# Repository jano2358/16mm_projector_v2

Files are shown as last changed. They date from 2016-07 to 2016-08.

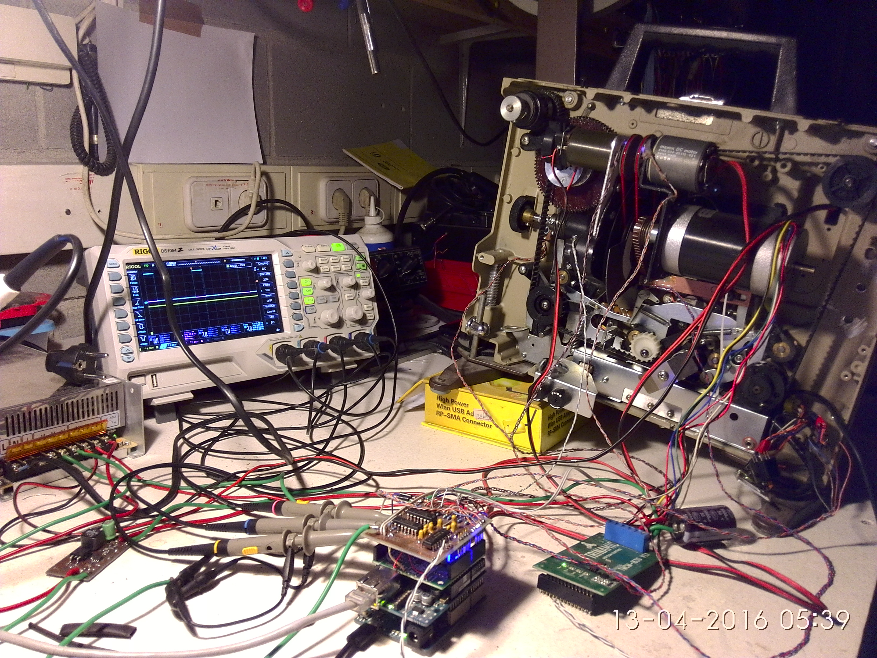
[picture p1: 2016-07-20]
photo_n_video/gen_view_unassembled.jpg

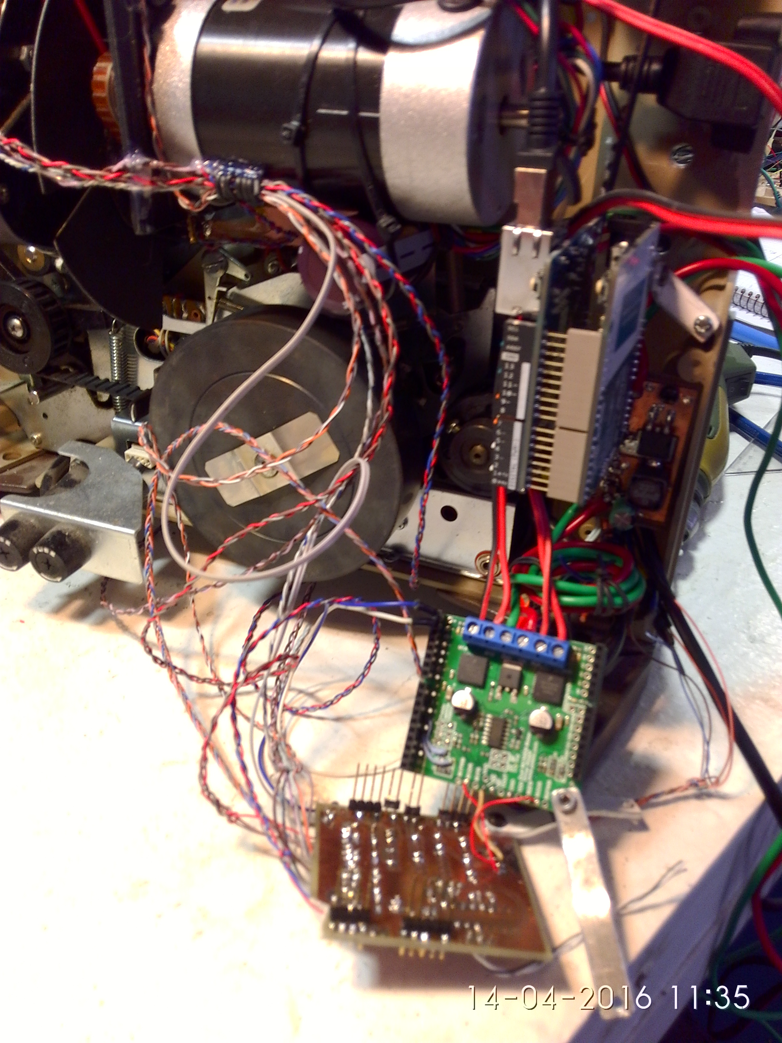
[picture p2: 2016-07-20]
photo_n_video/control_disassembly.jpg

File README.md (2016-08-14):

# 16mm_projector_v2
mod of a 16mm projector for the project "El curso del tiempo" from Xavi Hurtado

This is a modification of a projector (EIKI SSL0L) to take control over the parameters of the projection: tape speed, amount of light and shutter.
For the light we replace the incandescent bulb (300W, lumens: unknown)  by a COB LED (Citizen CLU058-1825C4-303M2K1, 100W about 17000 lumen).
To control the tape speed, We replaced the original motor with a DC brushless servo motor (Trinamic QBL5704-94-04-032 and TMCM-1630 control board).
The shutter originaly was hard linked to the main motor, we eliminated the hard link to have control independant, added a secondary shutter and two DC motors to move them. The link to the main motor and sync was made by a dual PLL system programed on an Arduino M0 board.
The power for these DC motors is delivered trough a Pololu board dual MC33296.
Arduino also controls the communication with the TMCM-1630 trough serial interface, the amount of light by switching the LED with a power
mosfet and receive the control from the computer over an ethernet line in OSC packets (we use here the Arduino Ethernet 2 Wiznet W5500).
The power is supplied by a Mean Well RSP-500-48 raised to 54V, with two DC-DC converters based on the TPS54560 chip from TI.

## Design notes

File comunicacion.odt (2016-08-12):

Variables de entrada:

Nombre | Tipo | Rango | Utilidad
/Vel_main | Int o Float | -43~43 (fps) | Velocidad del motor de arrastre, medida en frames por segundo
/Luz | Int | 0~255 | Potencia enviada a la lampara LED
/Vel_front | Int o Float | 0~150 (ops) | Velocidad del obturador frontal cuando es libre, medida en obturaciones por segundo.
/Vel_tras | Int o Float | 0~150 (ops) | Velocidad del obturador trasero cuando es libre.
/Master_front_tras | Int o Boolean | 0~1 | 0: el maestro del motor del obturador frontal es el Main 1: el maestro es el motor del obturador trasero
/Master_tras_front | Int o Boolean | 0~1 | 0: el maestro del motor del obturador trasero es el Main 1: el maestro es el motor del obturador frontal
/Front_free | Int o Boolean | 0~1 | 0: el motor del obturador frontal es esclavo 1: el motor es libre
/Tras_free | Int o Boolean | 0~1 | 0: el motor del obturador trasero es esclavo 1: el motor es libre
/Front_park | Int o Boolean | 0~1 | 0: indiferente 1: el motor del obturador frontal no es esclavo y se lleva a la posicion de parking.
/Tras_park | Int o Boolean | 0~1 | 0: indiferente 1: el motor del obturador trasero no es esclavo y se lleva a la posicion de parking.
/Div_front | Int o Float | 0~3 | Factor por el que se multiplicara la velocidad del motor del obturador frontal con respecto al maestro
/Div_tras | Int o Float | 0~3 | Factor por el que se multiplicara la velocidad del motor del obturador trasero con respecto al maestro
/Ph_f_target | Int o Float | 0~359 | Relacion de fase deseada para el motor del obturador frontal con respecto al maestro
/Ph_t_target | Int o Float | 0~359 | Relacion de fase desdeada para el motor del obturador trasero con respecto al maestro

Como acuse de dato recibido se retorna el mismo dato, en el caso de la velocidad del motor de arrastre de la cinta el dato se devuelve una vez que la placa Trinamic haya retornado los datos confirmados.

Los datos recibidos y retornados son del tipo OSC Message. El puerto de recepcion es 8000 y el de respuesta el 6000, la IP sera 172.26.100.177

Datos retornados cada 100mS:

Nombre | Tipo | Utilidad
/vel_obt_front_act | Float | Velocidad actual del obturador frontal
/vel_obt_tras_act | Float | Velocidad actual del obturador trasero
/ph_diff_front_act | Float | Diferencia de fase del obturador frontal actual respecto a su maestro.
/ph_diff_tras_act | Float | Diferencia de fase del obturador trasero actual respecto a su maestro.
/frame_count | Float | Cuenta de los cuadros pasados

Descripcion del sistema de control de los motores que mueven los obturadores:

El bloque de control basico es un sistema de lazo cerrado alimentando un PID con la velocidad deseada y la velocidad actual medida en la interrupcion correspondiente (estas interrupciones tienen una tasa de 11 pulsos por revolucion y son medidas en la polea solidaria con el motor en cuestion), la salida de PID es aplicada al PWM que alimenta el puente H de cada motor.

El siguiente nivel de control es un segundo lazo de realimentacion que tiene como entrada el resultado de la diferencia de tiempo entre el motor que sera esclavizado y su maestro, la salida se suma a la entrada de PID, en este caso los parametros Ki, Kp y Kd de PID estaran ajustados en una relacion aproximada 22:1 integral con respecto a proporcional, conformando un filtro de paso bajo. Si pensamos en el motor como un oscilador controlado por voltaje (PWM), la medicion de diferencia de tiempo es efectivamente un comparador de fase y la PID ajustada como filtro de paso bajo, el conjunto se puede ver como un PLL.

Uno de los tiempos que entran en el comparador de fase se multiplicara por un factor (/Div_front y /Div_tras respectivamente) para obtener una velocidad multiplicada como resultado pudiendo controlar de esta manera velocidades relativas al master diferentes a la unidad.

Un tercer lazo de realimentacion existe entre, la diferencia del tiempo medido directamente en cada obturador y el medido en quien sea su master, esta diferencia es expresada en grados (0~360) y sumada al tiempo que se le resta del maestro para obtener el error de la comparacion de entrada a PID, manejando una peticion de error en ese valor (entradas /Ph_f_target y /Ph_t_target)

conseguiremos un 'angulo' sumado al de referencia que proporciona el maestro. Este angulo se supervisa en el main loop y se corrige cuando se obtiene el valor de tiempo en cuestion.

Para seleccionar los estados se han colocado switches logicos con los que se permite seleccionar el origen de datos para el esclavo (/Master_tras front y /Master_front_tras) y si el motor en cuestion es libre o esclavo (/Front_free y /Tras_free), si el motor es libre el control sera su entrada de peticion de velocidad (/Vel_front y /Vel_tras).

Notas de utilizacion:

- la relacion de fase se mantiene con decencia en todo el rango central, en los extremos se puede perder la linealidad creando un bucle infinito de busqueda de fase, se recomienda mantener la fase en un rango 10º < Ph_x_target < 350º, en caso de que entre en bucle se puede salir de el con un requerimiento de fase un poco mas distanciado del extremo util

- la fase de entrada de los obturadores en pantalla es de180º para el obturador frontal y 170º para el obturador trasero, esto es medido con respecto al flanco de subida de la señal de sincronia del eje de arrastre de la cinta que coincide con el momento en el que se ha depositado un cuadro en la zona de proyeccion y la uña de arrastre va a por el siguiente

- a bajas velocidades las inercias del sistema son mas dificiles de controlar y afectan a la sincronia, tambien la tasa de datos se vuelve insuficiente hasta 6fps se soporta bien, por debajo de 5fps ya no es suficiente, si la sincronia desdeada es entre los obturadores, éste limite esta sobre los 12ops

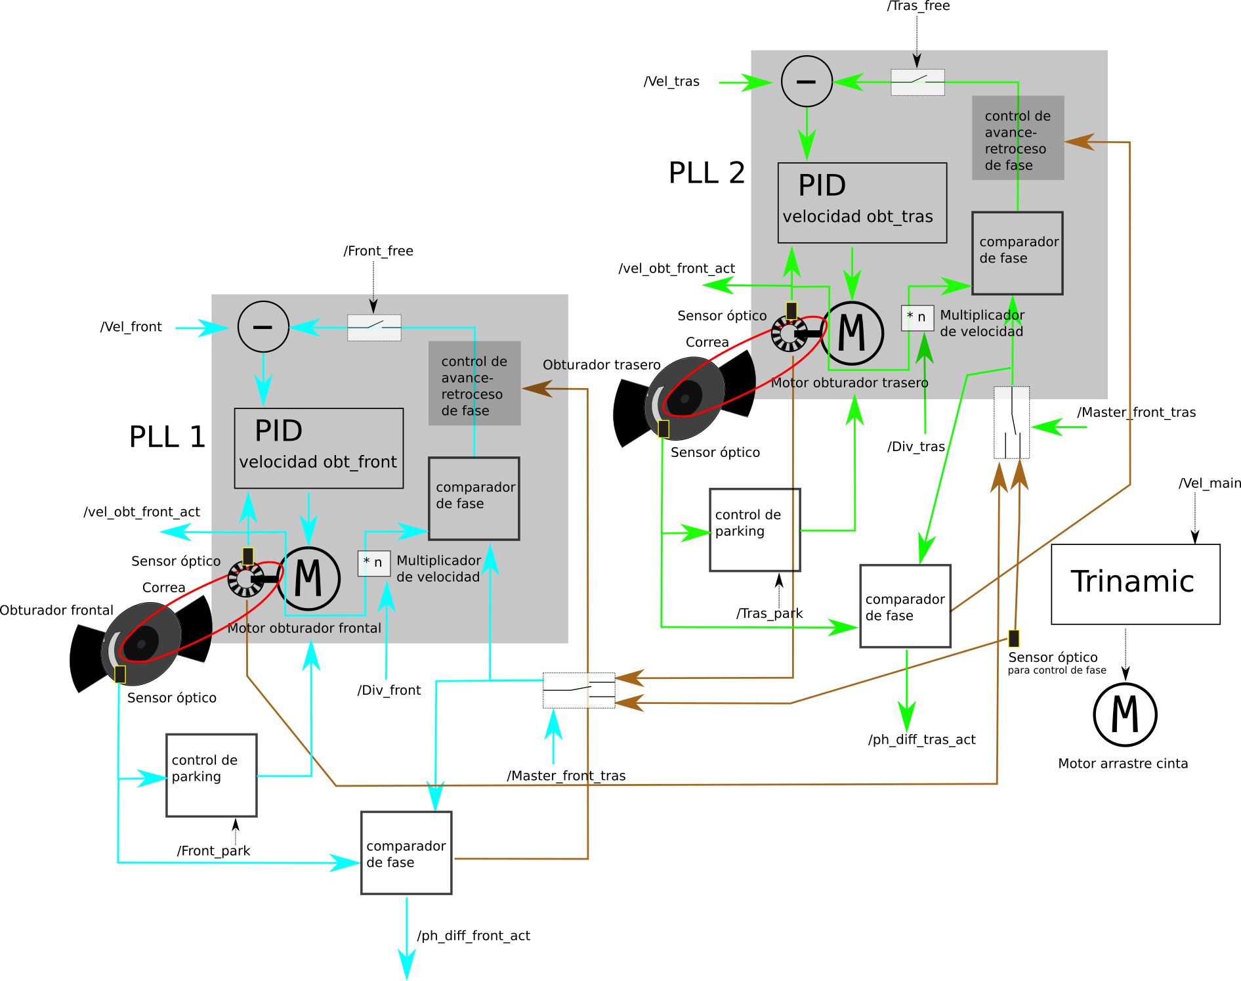
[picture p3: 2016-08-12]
Diagrama_de_bloques_0_2.png

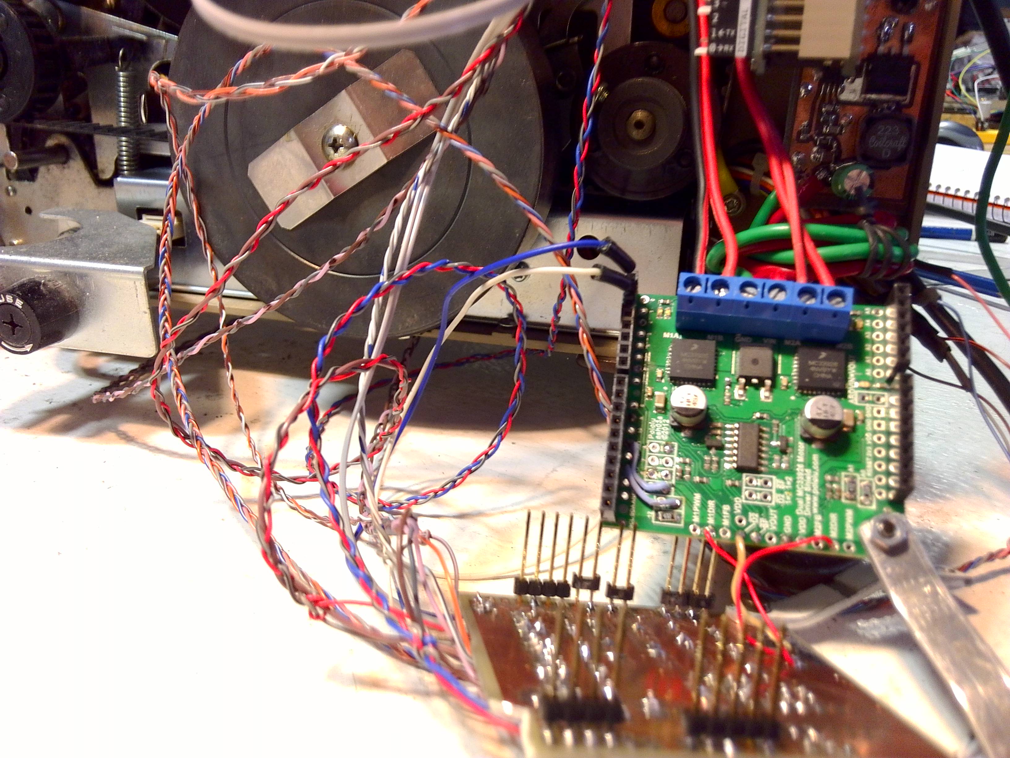
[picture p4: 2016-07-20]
photo_n_video/pololu_motor_control.jpg

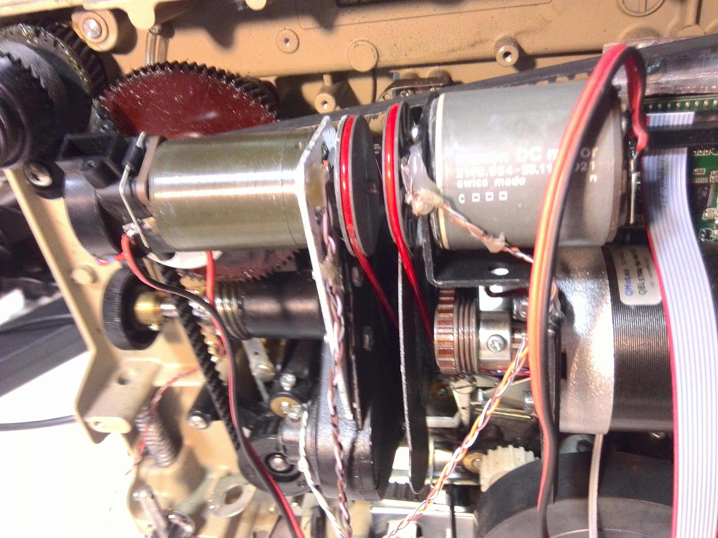
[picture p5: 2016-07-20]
photo_n_video/motors_close.jpg

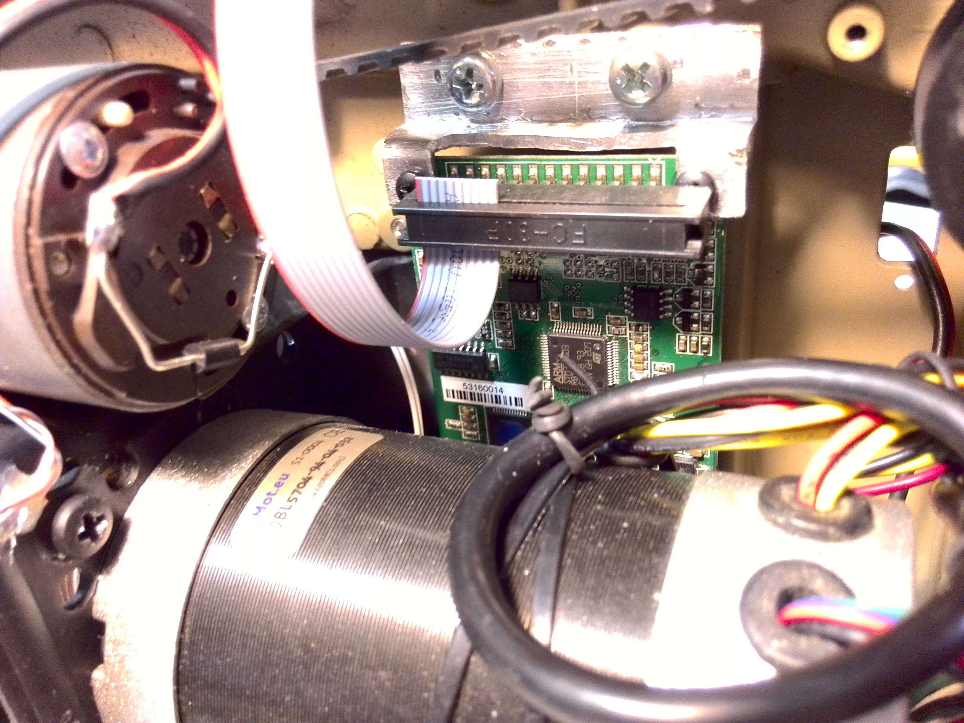
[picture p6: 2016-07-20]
photo_n_video/trinamic_board.jpg

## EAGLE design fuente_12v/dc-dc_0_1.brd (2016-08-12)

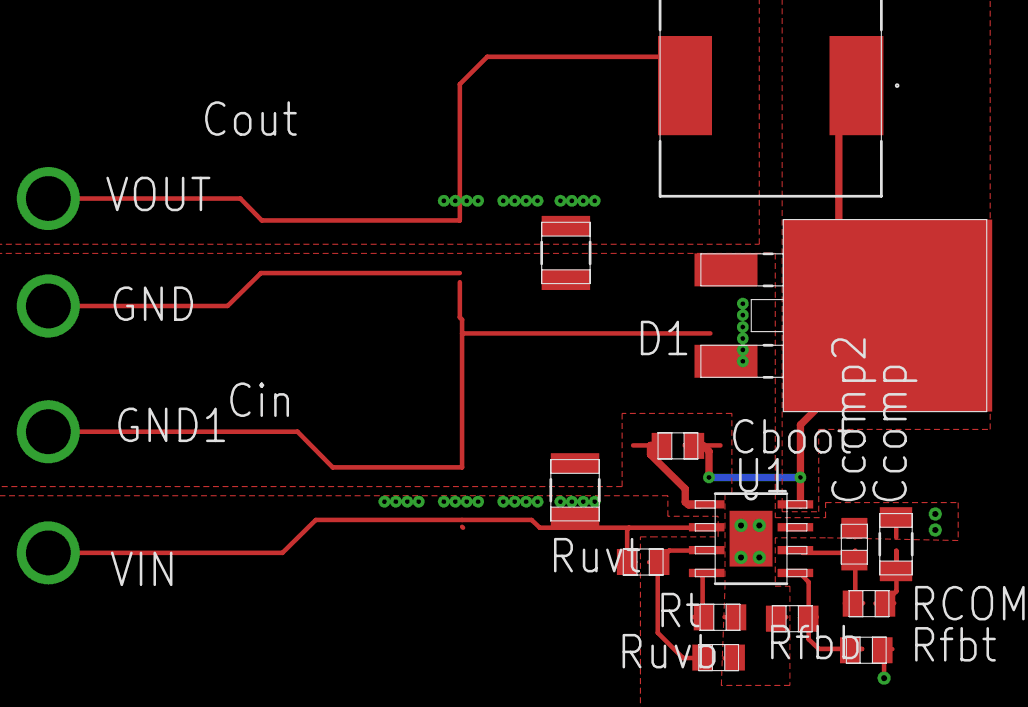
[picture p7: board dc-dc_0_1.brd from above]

Board: 4 copper layers, 18 parts (0 on the bottom side), 10 nets.

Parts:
Cboot: 0805
Ccomp: 1206
Ccomp2: 0805
Cin: 1210
Cout: 1210_280
D1: DDPAK
GND, GND1: TP-1502
L1: MSS1210
RCOMP: 0805
Rfbb: 0805
Rfbt: 0805
Rt: 0805
Ruvb: 0805
Ruvt: 0805
U1: R-PDSO-G8
VIN: TP-1502
VOUT: TP-1502

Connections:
0: Ccomp.2, Ccomp2.2, Cin.2, Cout.2, D1.1, D1.3, GND.1, GND1.1, Rfbb.2, Rt.2, Ruvb.2, U1.7, U1.9
1: Ccomp2.1, RCOMP.2, U1.6
2: Rt.1, U1.4
3: Cboot.1, U1.1
4: Rfbb.1, Rfbt.2, U1.5
5: Cboot.2, D1.2, L1.1, U1.8
6: Cin.1, Ruvt.1, U1.2, VIN.1
7: Cout.1, L1.2, Rfbt.1, VOUT.1
20: Ccomp.1, RCOMP.1
29: Ruvb.1, Ruvt.2, U1.3

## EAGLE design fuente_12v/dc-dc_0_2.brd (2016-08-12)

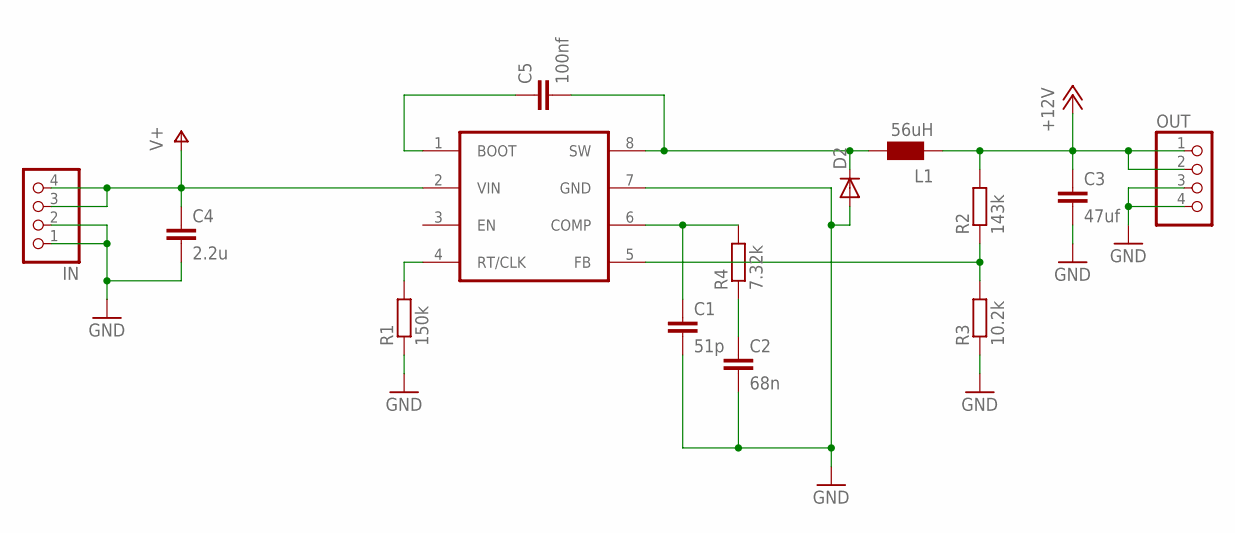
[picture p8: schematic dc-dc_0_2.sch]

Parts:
C1: 51p; C0805
C2: 68n; C1206
C3: 47uf; C1210
C4: 2.2u; C1210
C5: 100nf; C0805
D2: DIODE-DO-214AC; DO-214AC
IN: PINHD-1X4; 1X04
L1: 56uH; WE-PD_L/XL/XXL
OUT: PINHD-1X4; 1X04
R1: 150k; R0805
R2: 143k; R0805
R3: 10.2k; R0805
R4: 7.32k; R0805
U1: TPS54560; SO08-POWERPAD

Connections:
+12V: C3.1, L1.2 (1), OUT.1, OUT.2, R2.2
GND: C1.2, C2.2, C3.2, C4.2, D2.A, IN.1, IN.2, OUT.3, OUT.4, R1.1, R3.1, U1.7 (GND)
unnamed: C5.1, U1.1 (BOOT)
unnamed: C5.2, D2.C, L1.1 (2), U1.8 (SW)
unnamed: R2.1, R3.2, U1.5 (FB)
unnamed: C1.1, R4.2, U1.6 (COMP)
unnamed: C2.1, R4.1
unnamed: R1.2, U1.4 (RT/CLK)
V+: C4.1, IN.3, IN.4, U1.2 (VIN)

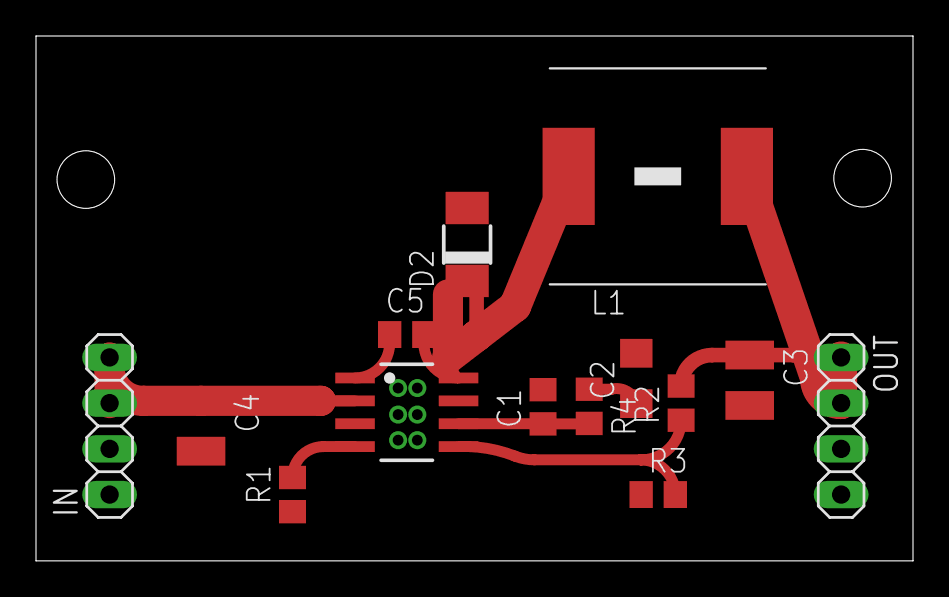
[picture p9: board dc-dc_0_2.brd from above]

Board: 2 copper layers, 48.7 x 29.2 mm, 14 parts (0 on the bottom side), 9 nets.

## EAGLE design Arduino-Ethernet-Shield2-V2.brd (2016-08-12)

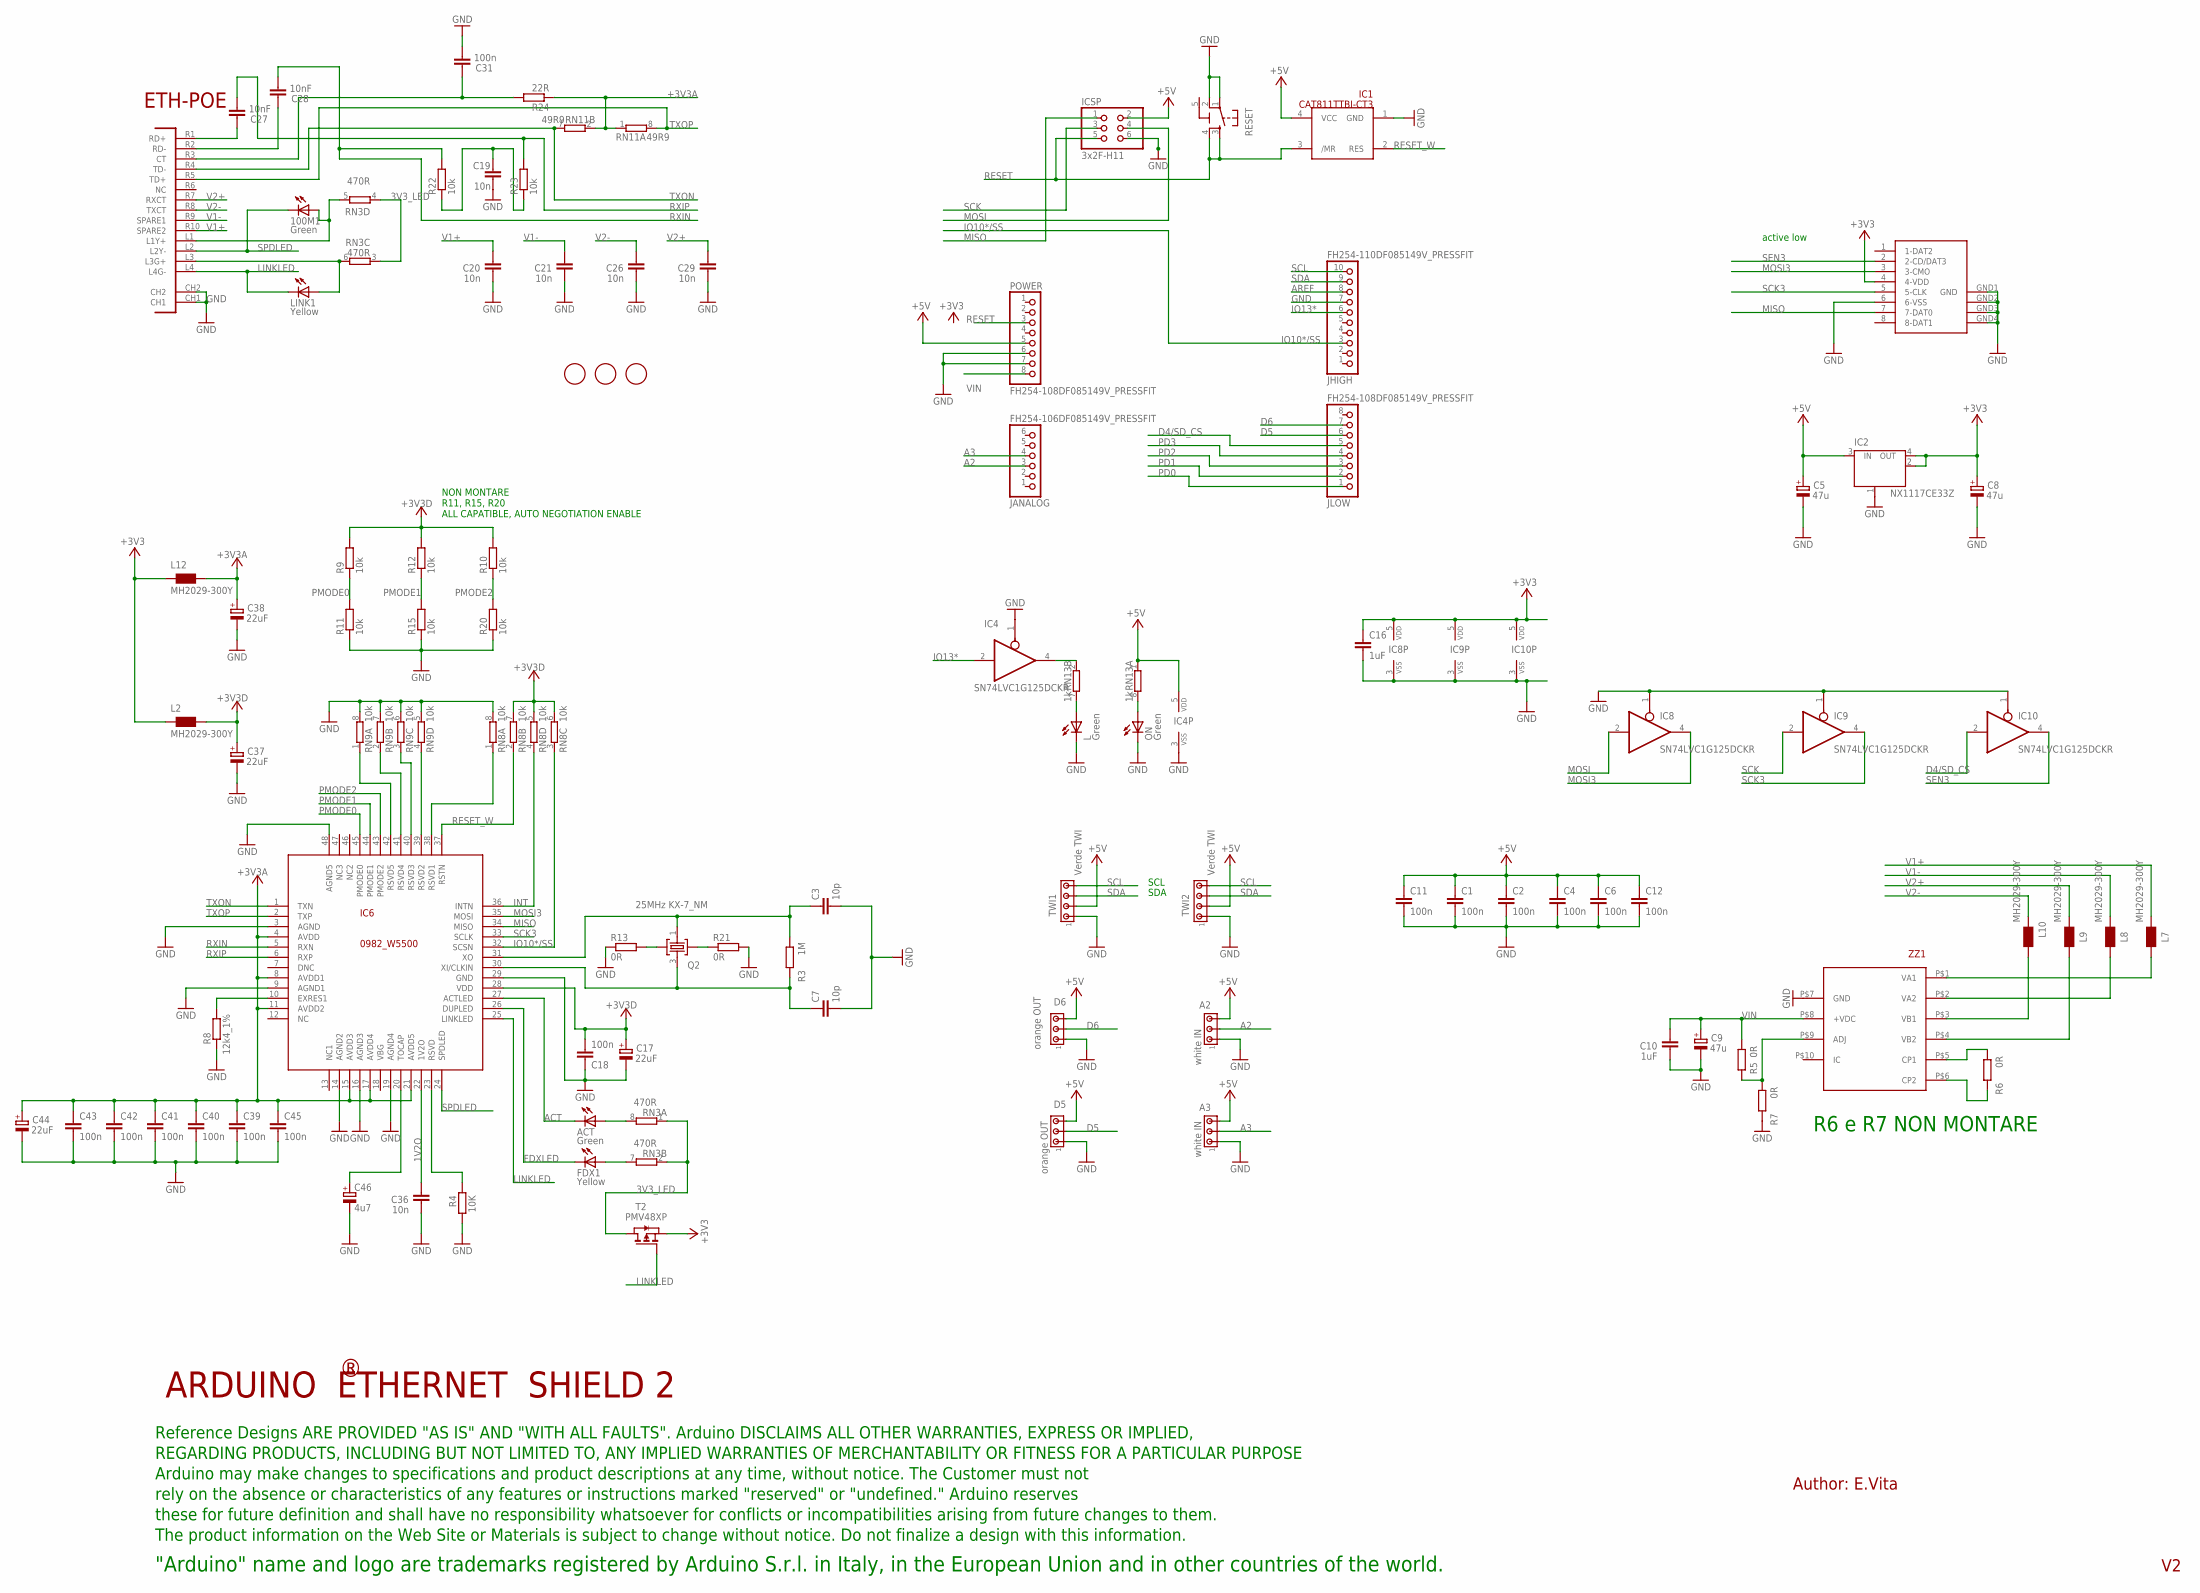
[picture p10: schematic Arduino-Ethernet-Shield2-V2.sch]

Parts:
100M1: Green; CHIPLED_0805
A2, A3: white IN; 10X03MTA
ACT: Green; CHIPLED_0805
C1, C2, C4, C6, C11, C12, C18, C31, C39, C40, C41, C42, C43, C45: 100n; C0603-ROUND
C3, C7: 10p; C0603-ROUND
C5, C8, C9: 47u; PANASONIC_D
C10, C16: 1uF; C0603-ROUND
C17, C37, C38, C44: 22uF; SMC_B
C19, C20, C21, C26, C29, C36: 10n; C0603-ROUND
C27, C28: 10nF; C0603-ROUND
C46: 4u7; SMC_A
D5, D6: orange OUT; 10X03MTA
FDX1: Yellow; CHIPLED_0805
FID2, FID3, FID4: FIDUCIALMOUNT; FIDUCIA-MOUNT
IC1: CAT811TTBI-CT3; SOT143
IC2: NX1117CE33Z; SOT223
IC4, IC8, IC9, IC10: SN74LVC1G125DCKR; SC70-5
IC6: 0982_W5500; TQFP48-7X7
ICSP: 3x2F-H11; 2X03
JANALOG: FH254-106DF085149V_PRESSFIT; 1X06-TH-PRESSFIT
JHIGH: FH254-110DF085149V_PRESSFIT; 1X10-TH-PRESSFIT
JLOW: FH254-108DF085149V_PRESSFIT; 1X08-TH-PRESSFIT
L: Green; CHIPLED_0805
L2, L7, L8, L9, L10, L12: MH2029-300Y; 0805
LINK1: Yellow; CHIPLED_0805
ON: Green; CHIPLED_0805
POWER: FH254-108DF085149V_PRESSFIT; 1X08-TH-PRESSFIT
Q2: 25MHz KX-7_NM; CRYSTAL3.2X2.5
R3: 1M; R0603-ROUND
R4: 10K; R0603-ROUND
R5, R6, R7: 0R; R0603-ROUND
R8: 12k4_1%; R0603-ROUND
R9, R10, R11, R12, R15, R20, R22, R23: 10k; R0603-ROUND
R13, R21: 0R; R0402
R24: 22R; R0603-ROUND
RESET: 0946_TS42031-160W-TR-7260; TS42
RN3: 470R; CAY16
RN8, RN9: 10k; CAY16
RN11: 49R9; CAY16
RN13: 1k; CAY16
T2: PMV48XP; SOT-23; PART_NUMBER PMV48XP
TWI1, TWI2: Verde TWI; 10X04MTA
U$1: DISCLAIMER
UC1: RB1-125BHQ1A; POE-RJ45
X1: 0046_15TW-882; SDCARD-15TW-8821
ZZ1: 0343_AG9612-2BR; AG9000

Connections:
1V2O: C36.2, IC6.22 (1V2O)
3V3_LED: RN3.1, RN3.2 (1), RN3.3 (1), RN3.4 (1), T2.1 (D)
5-GND: RESET.5 (5-GND)
+3V3: C8.+, C16.1, IC2.2 (OUT), IC2.4 (OUT), IC8.5 (VDD), IC9.5 (VDD), IC10.5 (VDD), L2.1, L12.1, T2.2 (S), X1.4 (4-VDD)
+3V3A: C38.+, C39.1, C40.1, C41.1, C42.1, C43.1, C44.+, C45.1, IC6.4 (AVDD), IC6.8 (AVDD1), IC6.11 (AVDD2), IC6.15 (AVDD3), IC6.17 (AVDD4), IC6.21 (AVDD5), L12.2, R24.1, RN11.1, RN11.2 (1)
+3V3D: C17.+, C18.2, C37.+, IC6.28 (VDD), L2.2, R9.2, R10.2, R12.2, RN8.5 (2), RN8.6 (2), RN8.7 (2)
+5V: A2.3, A3.3, C1.1, C2.1, C4.1, C5.+, C6.1, C11.1, C12.1, D5.3, D6.3, IC1.4 (VCC), IC2.3 (IN), IC4.5 (VDD), ICSP.2, POWER.5, RN13.1, TWI1.2, TWI2.2
A2: A2.2, JANALOG.3
A3: A3.2, JANALOG.4
ACT: ACT.C, IC6.27 (ACTLED)
AREF: JHIGH.8
D4/SD_CS: IC10.2 (I), JLOW.5
D5: D5.2, JLOW.6
D6: D6.2, JLOW.7
FDXLED: FDX1.C, IC6.26 (DUPLED)
GND: A2.1, A3.1, C1.2, C2.2, C3.2, C4.2, C5.-, C6.2, C7.2, C8.-, C9.-, C10.1, C11.2, C12.2, C16.2, C17.-, C18.1, C19.1, C20.1, C21.1, C26.1, C29.1, C31.1, C36.1, C37.-, C38.-, C39.2, C40.2, C41.2, C42.2, C43.2, C44.-, C45.2, C46.-, D5.1, D6.1, IC1.1 (GND), IC2.1 (GND/ADJ), IC4.1 (OE), IC4.3 (VSS), IC6.3 (AGND), IC6.9 (AGND1), IC6.14 (AGND2), IC6.16 (AGND3), IC6.19 (AGND4), IC6.29 (GND), IC6.48 (AGND5), IC8.1 (OE), IC8.3 (VSS), IC9.1 (OE), IC9.3 (VSS), IC10.1 (OE), IC10.3 (VSS), ICSP.6, JHIGH.7, L.C, ON.C, POWER.6, POWER.7, R4.1, R7.2, R8.1, R11.1, R13.1, R15.1, R20.1, R21.2, RESET.1, RESET.2, RN8.8 (2), RN9.5 (2), RN9.6 (2), RN9.7 (2), RN9.8 (2), TWI1.1, TWI2.1, UC1.CH1, UC1.CH2, X1.6 (6-VSS), X1.GND1 (GND), X1.GND2 (GND1), X1.GND3 (GND2), X1.GND4 (GND3), ZZ1.P$7 (GND)
INT: IC6.36 (INTN), RN8.4 (1)
IO10*/SS: IC6.32 (SCSN), JHIGH.3, RN8.3 (1)
IO13*: IC4.2 (I), JHIGH.6
LINKLED: IC6.25 (LINKLED), LINK1.C, T2.3 (G), UC1.L4 (L4G-)
MISO: IC6.34 (MISO), ICSP.1, X1.7 (7-DAT0)
MOSI: IC8.2 (I), ICSP.4
MOSI3: IC6.35 (MOSI), IC8.4 (O), X1.3 (3-CMO)
unnamed: L7.2, ZZ1.P$1 (VA1)
unnamed: L8.2, ZZ1.P$2 (VA2)
unnamed: L9.2, ZZ1.P$4 (VB2)
unnamed: L10.2, ZZ1.P$3 (VB1)
unnamed: C3.1, IC6.31 (XO), Q2.1, R3.1
unnamed: IC6.39 (RSVD2), RN9.4 (1)
unnamed: ACT.A, RN3.8 (2)
unnamed: Q2.2, R13.2
unnamed: Q2.4, R21.1
unnamed: LINK1.A, RN3.6 (2), UC1.L3 (L3G+)
unnamed: IC6.23 (RSVD), R4.2
unnamed: 100M1.A, RN3.5 (2), UC1.L1 (L1Y+)
unnamed: C19.2, R22.1, R23.1
unnamed: C27.2, UC1.R1 (RD+)
unnamed: C28.2, UC1.R2 (RD-)
unnamed: FDX1.A, RN3.7 (2)
unnamed: IC6.40 (RSVD3), RN9.3 (1)
unnamed: R6.1, ZZ1.P$5 (CP1)
unnamed: R6.2, ZZ1.P$6 (CP2)
unnamed: R5.2, R7.1, ZZ1.P$9 (ADJ)
unnamed: IC6.41 (RSVD4), RN9.2 (1)
unnamed: C31.2, R24.2, UC1.R3 (CT)
unnamed: IC6.42 (RSVD5), RN9.1
unnamed: C46.+, IC6.20 (TOCAP)
unnamed: IC6.38 (RSVD1), RN8.1
unnamed: IC6.10 (EXRES1), R8.2
unnamed: ON.A, RN13.8 (2)
unnamed: IC4.4 (O), RN13.2 (1)
unnamed: L.A, RN13.7 (2)
NC: IC6.12 (NC)
OSC2E2: C7.1, IC6.30 (XI/CLKIN), Q2.3, R3.2
PD0: JLOW.1
PD1: JLOW.2
PD2: JLOW.3
PD3: JLOW.4
PMODE0: IC6.45 (PMODE0), R9.1, R11.2
PMODE1: IC6.44 (PMODE1), R12.1, R15.2
PMODE2: IC6.43 (PMODE2), R10.1, R20.2
RESET: IC1.3 (/MR), ICSP.5, POWER.3, RESET.3, RESET.4
RESET_W: IC1.2 (RES), IC6.37 (RSTN), RN8.2 (1)
RXIN: C28.1, IC6.5 (RXN), R22.2
RXIP: C27.1, IC6.6 (RXP), R23.2
SCK: IC9.2 (I), ICSP.3
SCK3: IC6.33 (SCLK), IC9.4 (O), X1.5 (5-CLK)
SCL: JHIGH.10, TWI1.4, TWI2.4
SDA: JHIGH.9, TWI1.3, TWI2.3
SEN3: IC10.4 (O), X1.2 (2-CD/DAT3)
SPDLED: 100M1.C, IC6.24 (SPDLED), UC1.L2 (L2Y-)
TXON: IC6.1 (TXN), RN11.7 (2), UC1.R4 (TD-)
TXOP: IC6.2 (TXP), RN11.8 (2), UC1.R5 (TD+)
V1+: C20.2, L7.1, UC1.R10 (SPARE2)
V1-: C21.2, L8.1, UC1.R9 (SPARE1)
V2+: C29.2, L9.1, UC1.R7 (RXCT)
V2-: C26.2, L10.1, UC1.R8 (TXCT)
VIN: C9.+, C10.2, POWER.8, R5.1, ZZ1.P$8 (+VDC)

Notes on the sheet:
active low
NON MONTARE R11, R15, R20 ALL CAPATIBLE, AUTO NEGOTIATION ENABLE
ETH-POE
SCL
SDA
R6 e R7 NON MONTARE
ARDUINO ETHERNET SHIELD 2
Author: E.Vita

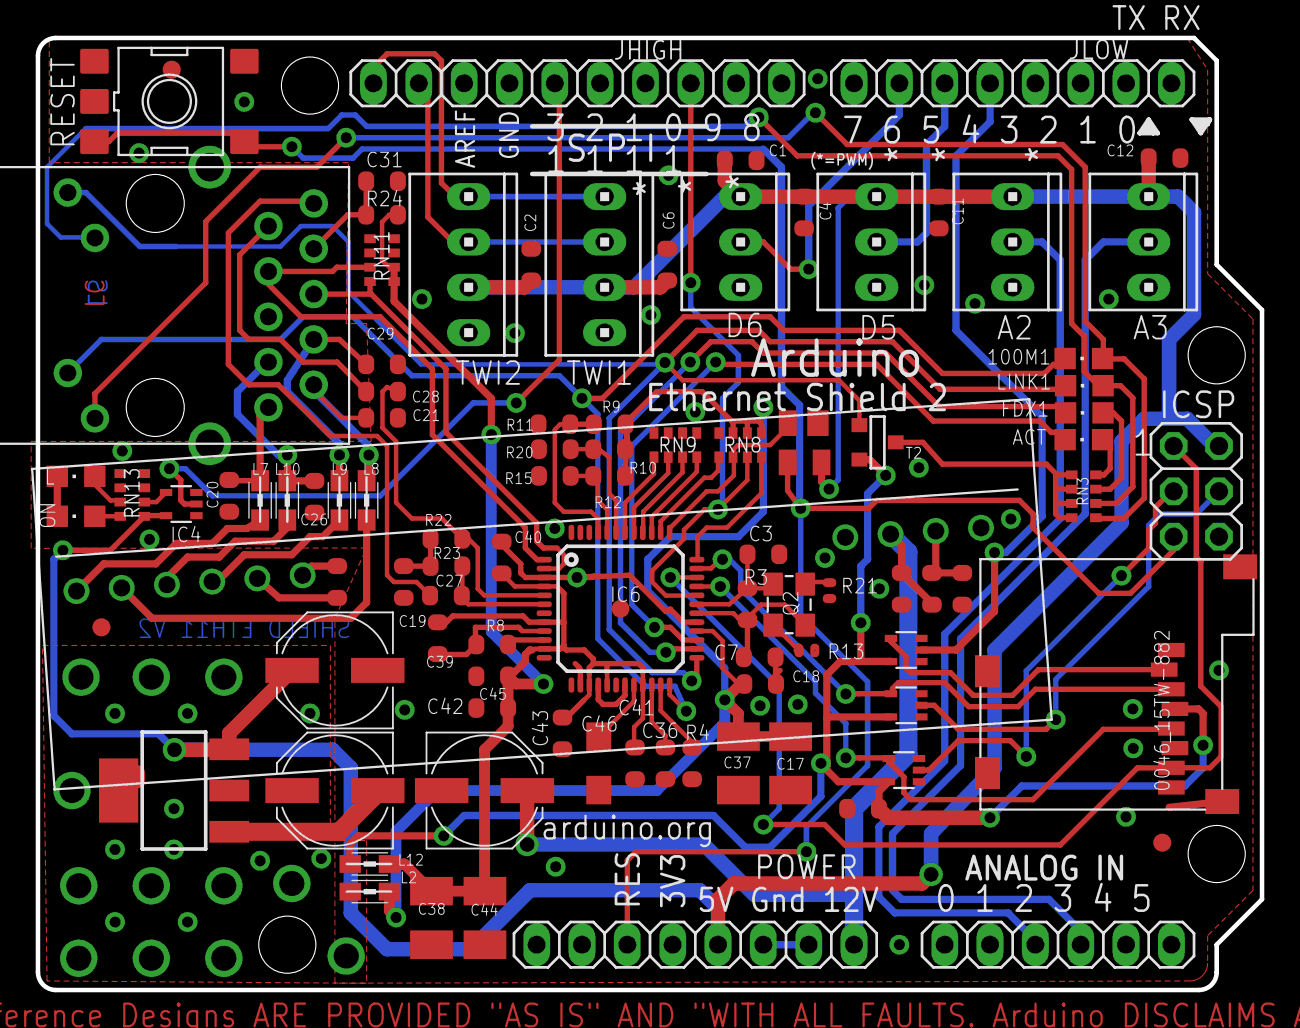
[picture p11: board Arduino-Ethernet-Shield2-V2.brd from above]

Board: 2 copper layers, 68.6 x 53.3 mm, 96 parts (0 on the bottom side), 71 nets.

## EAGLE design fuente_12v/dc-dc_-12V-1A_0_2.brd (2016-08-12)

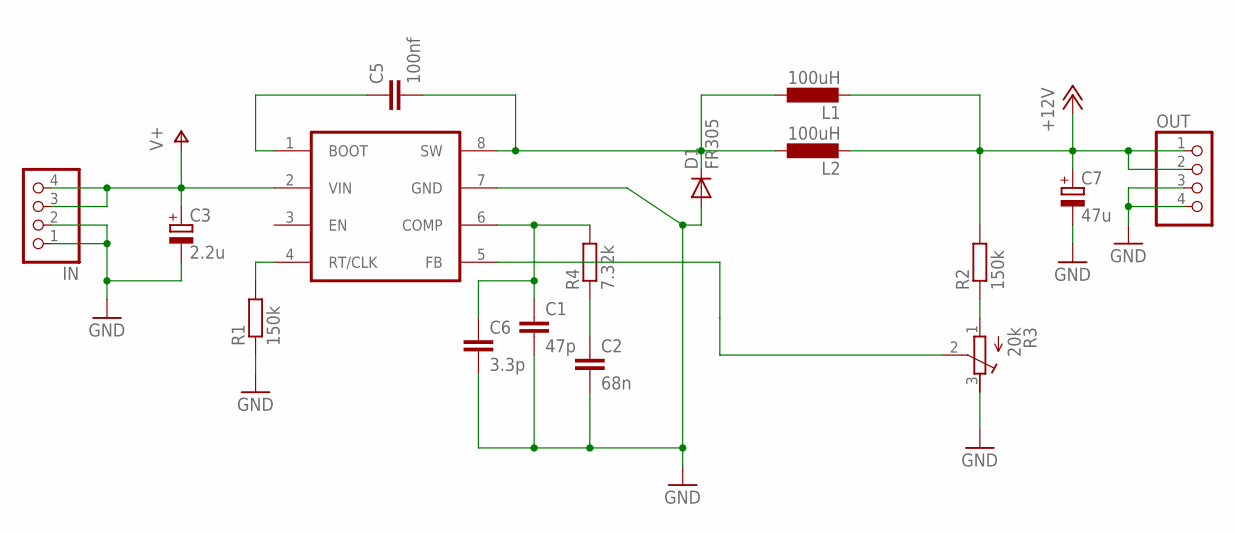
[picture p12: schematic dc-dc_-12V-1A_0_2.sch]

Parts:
C1: 47p; C1206
C2: 68n; C1206
C3: 2.2u; E2-4
C5: 100nf; C0805
C6: 3.3p; C1206
C7: 47u; E2-4
D1: FR305; DO201-15
IN: PINHD-1X4; 1X04
L1, L2: 100uH; RCL_6000-XXXX-RC
OUT: PINHD-1X4; 1X04
R1, R2: 150k; R0805
R3: 20k; RTRIM64X
R4: 7.32k; 0204/5
U1: TPS54560; SO08-POWERPAD

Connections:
+12V: C7.+, L1.2, L2.2, OUT.1, OUT.2, R2.2
GND: C1.2, C2.2, C3.-, C6.2, C7.-, D1.A, IN.1, IN.2, OUT.3, OUT.4, R1.1, R3.3 (A), U1.7 (GND)
unnamed: C5.1, U1.1 (BOOT)
unnamed: C5.2, D1.C, L1.1, L2.1, U1.8 (SW)
unnamed: R2.1, R3.1 (E)
unnamed: R3.2 (S), U1.5 (FB)
unnamed: C1.1, C6.1, R4.2, U1.6 (COMP)
unnamed: C2.1, R4.1
unnamed: R1.2, U1.4 (RT/CLK)
V+: C3.+, IN.3, IN.4, U1.2 (VIN)

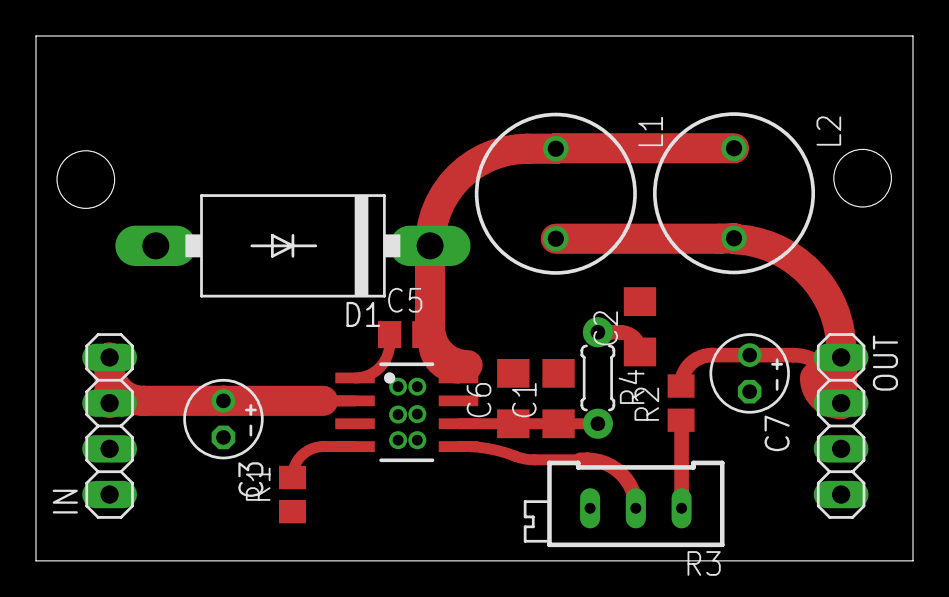
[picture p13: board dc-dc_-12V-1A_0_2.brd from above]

Board: 2 copper layers, 48.7 x 29.2 mm, 16 parts (0 on the bottom side), 10 nets.

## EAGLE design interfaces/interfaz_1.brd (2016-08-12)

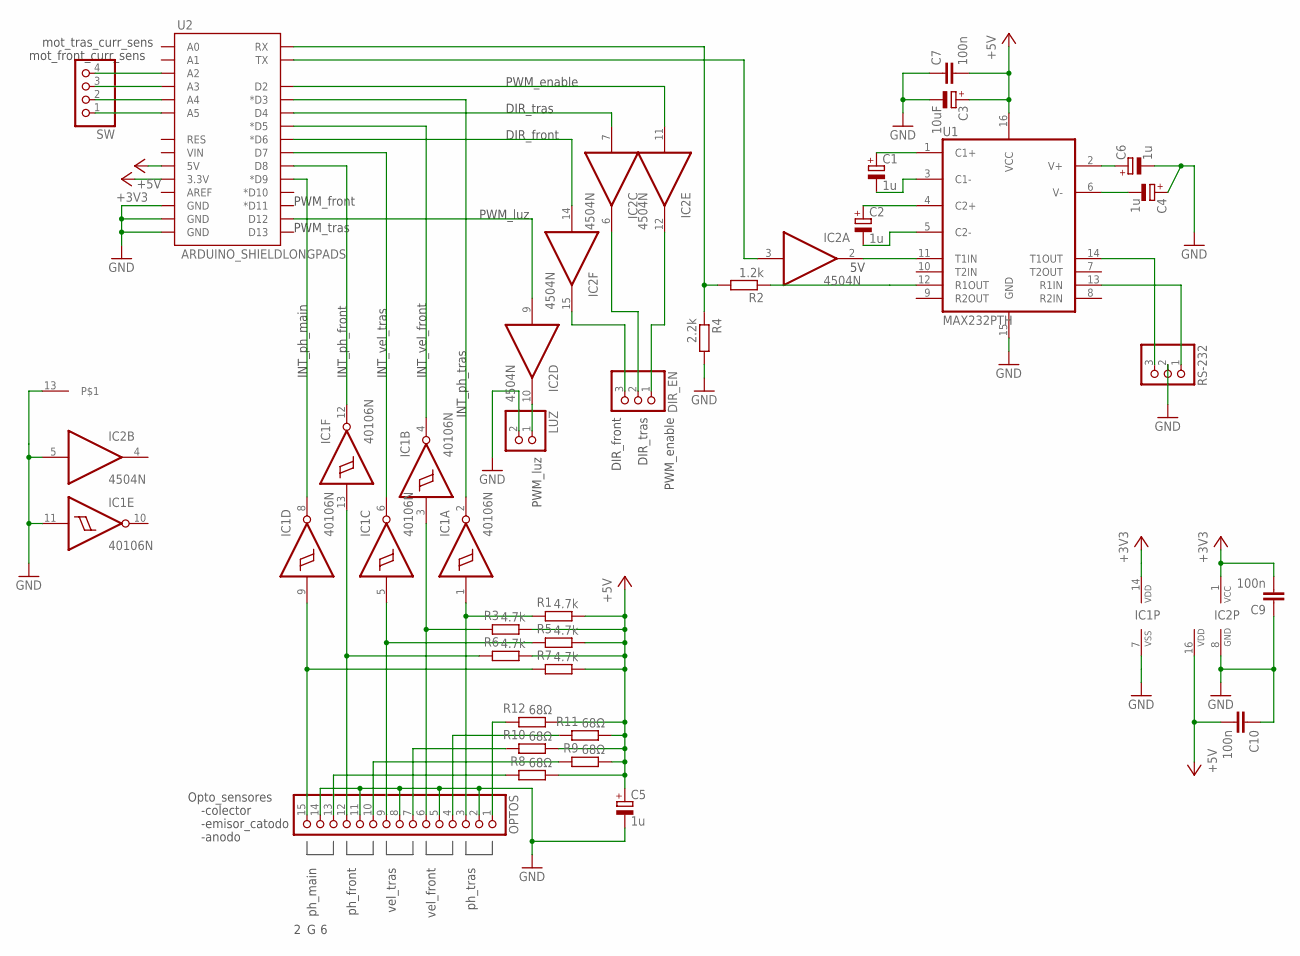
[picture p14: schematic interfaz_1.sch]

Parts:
C1, C2, C4, C5, C6: 1u; E2-4
C3: 10uF; E2-4
C7, C9, C10: 100n; C025-025X050
DIR_EN: PINHD-1X3; 1X03
IC1: 40106N; DIL14
IC2: 4504N; DIL16
LUZ: PINHD-1X2; 1X02
OPTOS: PINHD-1X15; 1X15
R1, R3, R5, R6, R7: 4.7k; 0204/5
R2: 1.2k; 0204/5
R4: 2.2k; 0204/5
R8, R9, R10, R11, R12: 68Ω; 0204/5
RS-232: PINHD-1X3; 1X03
SW: PINHD-1X4; 1X04
U1: MAX232PTH; DIL16
U2: ARDUINO_SHIELDLONGPADS; DUEMILANOVE_SHIELD_LONGPADS

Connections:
+3V3: C9.2, IC1.14 (VDD), IC2.1 (VCC), U2.3.3V
+5V: C3.+, C5.+, C7.2, C10.2, IC2.16 (VDD), R1.1, R3.1, R5.1, R6.1, R7.1, R8.1, R9.1, R10.1, R11.1, R12.1, U1.16 (VCC), U2.5V
GND: C3.-, C4.+, C5.-, C6.-, C7.1, C9.1, C10.1, IC1.7 (VSS), IC1.11 (I), IC2.5 (I), IC2.8 (GND), IC2.13, LUZ.2, OPTOS.2, OPTOS.5, OPTOS.8, OPTOS.11, OPTOS.14, R4.2, RS-232.2, U1.15 (GND), U2.GND@0 (GND), U2.GND@1 (GND), U2.GND@2 (GND)
unnamed: C1.+, U1.1 (C1+)
unnamed: C1.-, U1.3 (C1-)
unnamed: C2.+, U1.4 (C2+)
unnamed: C2.-, U1.5 (C2-)
unnamed: C4.-, U1.6 (V-)
unnamed: C6.+, U1.2 (V+)
unnamed: RS-232.1, U1.13 (R1IN)
unnamed: IC2.11 (I), U2.D2
unnamed: IC2.3 (I), U2.TX
unnamed: R2.1, U1.12 (R1OUT)
unnamed: R2.2, R4.1, U2.RX
unnamed: IC2.2 (O), U1.11 (T1IN)
unnamed: DIR_EN.1, IC2.12 (O)
unnamed: RS-232.3, U1.14 (T1OUT)
unnamed: IC2.7 (I), U2.D4
unnamed: DIR_EN.2, IC2.6 (O)
unnamed: IC2.14 (I), U2.D6 (*D6)
unnamed: DIR_EN.3, IC2.15 (O)
unnamed: IC2.9 (I), U2.D12
unnamed: IC2.10 (O), LUZ.1
unnamed: IC1.3 (I), OPTOS.6, R3.2
unnamed: IC1.2 (O), U2.D3 (*D3)
unnamed: IC1.4 (O), U2.D5 (*D5)
unnamed: IC1.6 (O), U2.D7
unnamed: IC1.12 (O), U2.D8
unnamed: IC1.8 (O), U2.D9 (*D9)
unnamed: IC1.1 (I), OPTOS.3, R1.2
unnamed: IC1.5 (I), OPTOS.9, R5.2
unnamed: IC1.13 (I), OPTOS.12, R6.2
unnamed: IC1.9 (I), OPTOS.15, R7.2
unnamed: OPTOS.13, R8.2
unnamed: OPTOS.10, R9.2
unnamed: OPTOS.7, R10.2
unnamed: OPTOS.4, R11.2
unnamed: OPTOS.1, R12.2
unnamed: SW.1, U2.A5
unnamed: SW.2, U2.A4
unnamed: SW.3, U2.A3
unnamed: SW.4, U2.A2

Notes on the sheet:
PWM_enable
DIR_tras
DIR_front
PWM_luz
PWM_tras
PWM_front
INT_vel_tras
INT_vel_front
INT_ph_tras
INT_ph_front
INT_ph_main
Opto_sensores
-colector
-emisor_catodo
-anodo
ph_main
ph_front
ph_tras
vel_front
vel_tras
mot_tras_curr_sens
mot_front_curr_sens

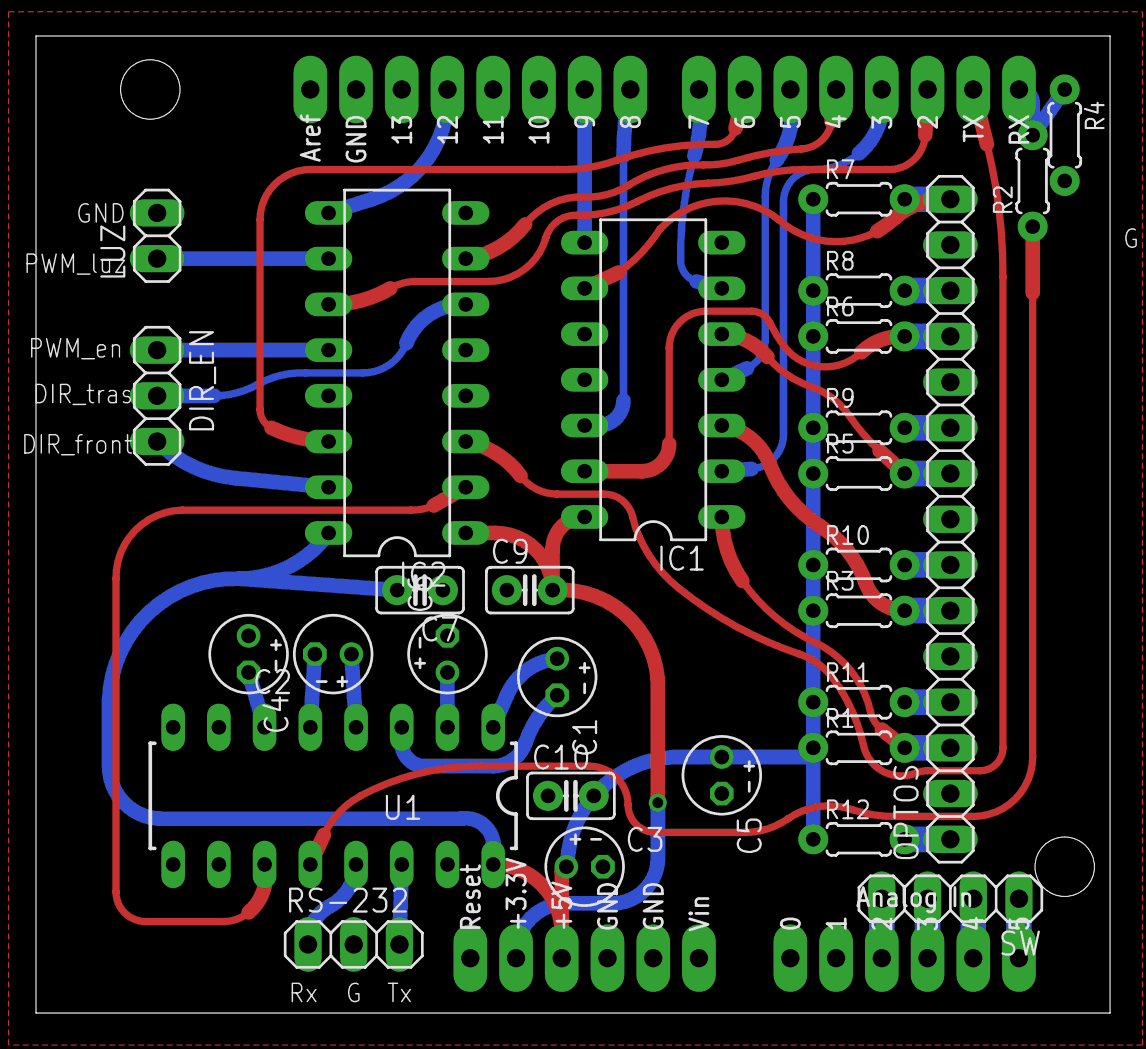
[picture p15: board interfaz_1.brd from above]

Board: 2 copper layers, 59.7 x 54.3 mm, 30 parts (0 on the bottom side), 42 nets.

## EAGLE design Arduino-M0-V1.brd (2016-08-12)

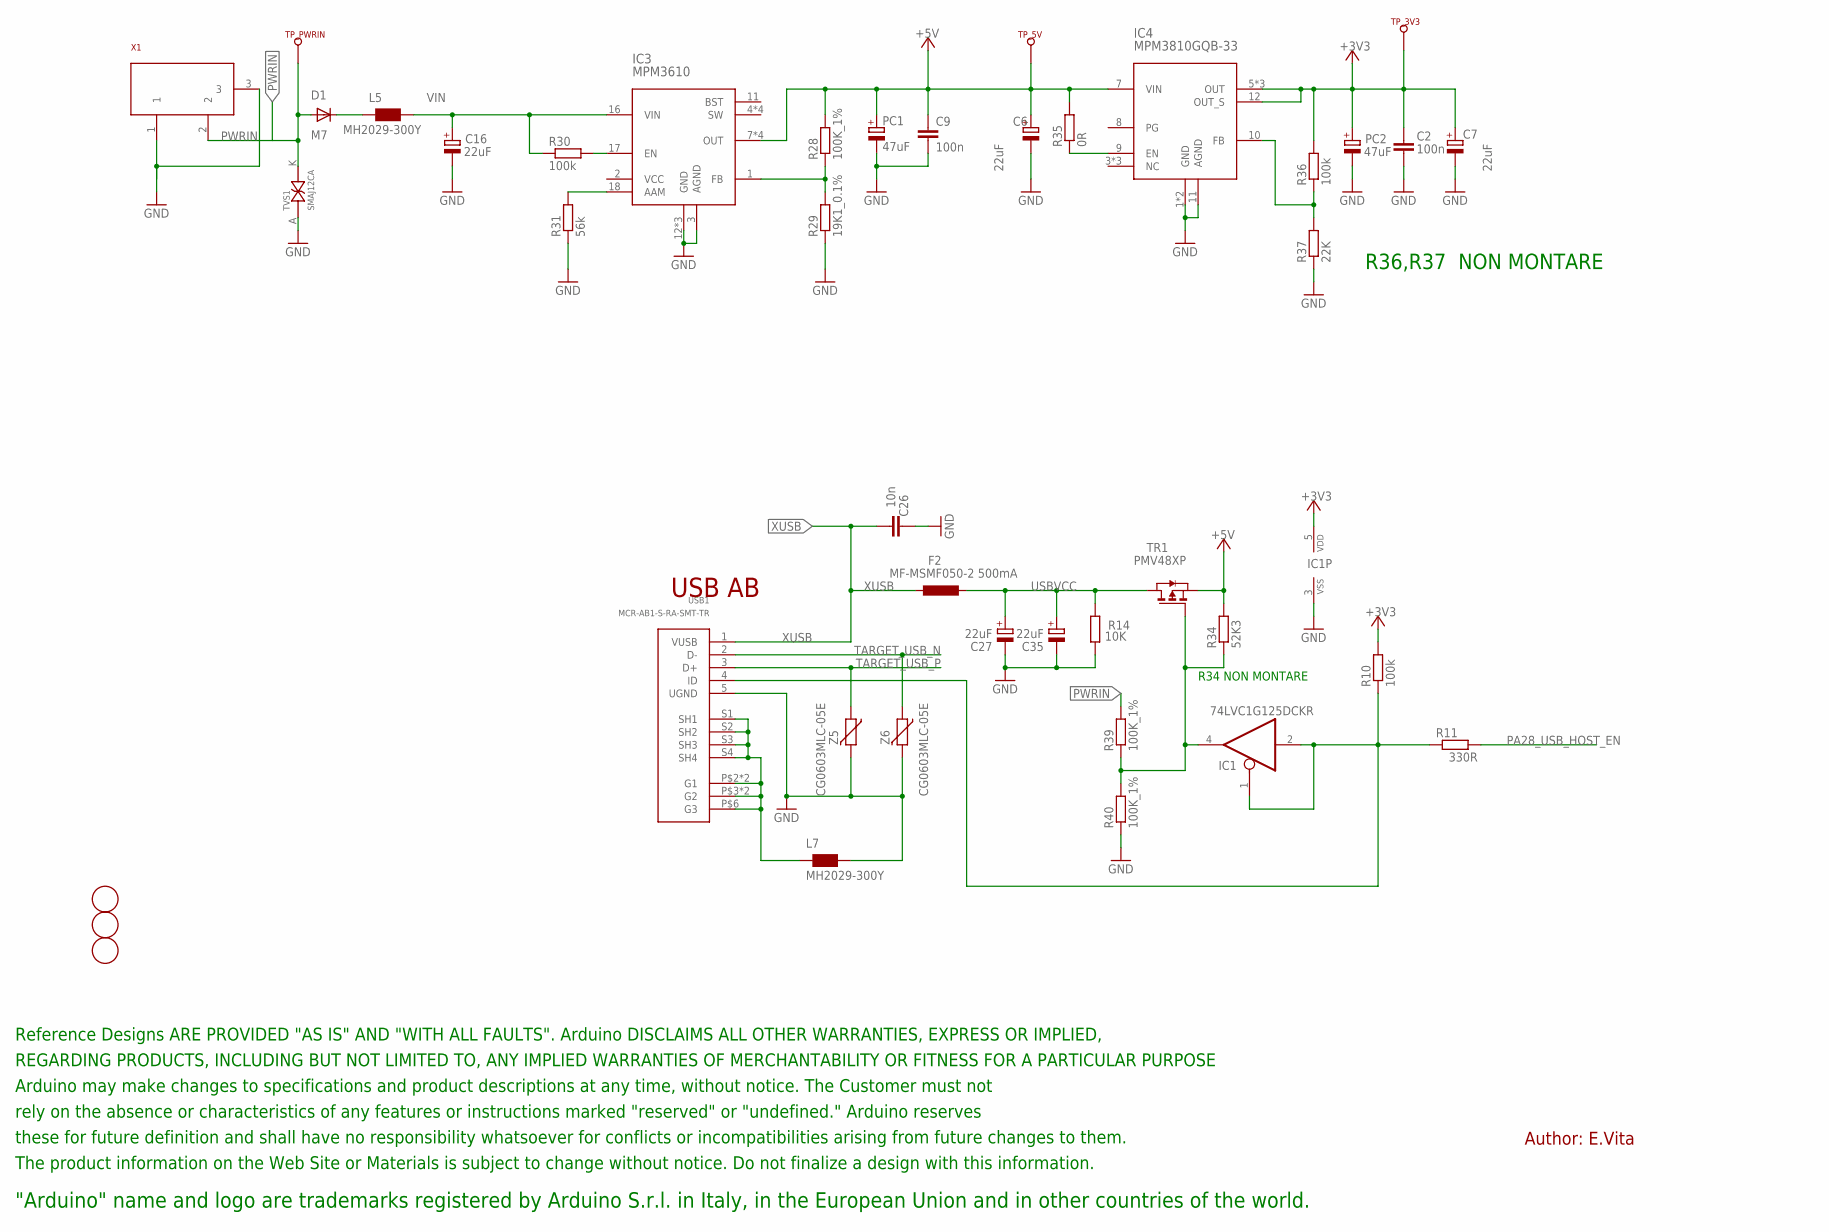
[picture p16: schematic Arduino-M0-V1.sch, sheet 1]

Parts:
C2, C9: 100n; C0603-ROUND
C6, C7, C16, C27, C35: 22uF; SMC_B
C26: 10n; C0603-ROUND
D1: M7; SMB
F2: MF-MSMF050-2 500mA; L1812
FD1, FD2, FD3: FIDUCIALMOUNT; FIDUCIA-MOUNT
IC1: 74LVC1G125DCKR; SC70-5
IC3: MPM3610; QFN-20
IC4: MPM3810GQB-33; QFN-12
L5, L7: MH2029-300Y; 0805
PC1, PC2: 47uF; PANASONIC_D
R10, R30, R36: 100k; R0603-ROUND
R11: 330R; R0603-ROUND
R14: 10K; R0603-ROUND
R28, R39, R40: 100K_1%; R0603-ROUND
R29: 19K1_0.1%; R0603-ROUND
R31: 56k; R0603-ROUND
R34: 52K3; R0603-ROUND
R35: 0R; R0603-ROUND
R37: 22K; R0603-ROUND
TP_3V3, TP_5V: TP_SP; TP-SP
TP_PWRIN: TP_SP; TP-SP
TR1: PMV48XP; SOT-23
TVS1: SMAJ12CA; SMA-TVS
U$1: DISCLAIMER-SMALL; DISCLAIMER
USB1: MCR-AB1-S-RA-SMT-TR; MCR-AB1-S-RA-SMT-SINGLHOLES
X1: 0018_19746-POWER-SUPPLY; POWERSUPPLY_DC-21MM
Z5, Z6: CG0603MLC-05E; CT/CN0603

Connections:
+3V3: C2.2, C7.+, IC1.5 (VDD), IC4.5 (OUT), IC4.6 (OUT), IC4.12 (OUT_S), IC4.14 (OUT), PC2.+, R10.2, R36.2, TP_3V3.X; also elsewhere on the board
+5V: C6.+, C9.1, IC3.7 (OUT), IC3.8 (OUT), IC3.9 (OUT), IC3.20 (OUT), IC4.7 (VIN), PC1.+, R28.2, R34.2, R35.2, TP_5V.X, TR1.2 (S); also elsewhere on the board
GND: C2.1, C6.-, C7.-, C9.2, C16.-, C26.2, C27.-, C35.-, IC1.3 (VSS), IC3.3 (AGND), IC3.12 (GND), IC3.13 (GND), IC3.14 (GND), IC4.1 (GND), IC4.2 (GND), IC4.11 (AGND), L7.2, PC1.-, PC2.-, R14.1, R29.1, R31.1, R37.1, R40.1, TVS1.A (AK), USB1.5 (UGND), X1.1, X1.3, Z5.2, Z6.2; also elsewhere on the board
unnamed: IC1.4 (O), R34.1, R39.1, R40.2, TR1.3 (G)
unnamed: IC1.1 (OE), IC1.2 (I), R10.1, R11.1, USB1.4 (ID)
unnamed: D1.C, L5.1
unnamed: IC4.9 (EN), R35.1
unnamed: IC4.10 (FB), R36.1, R37.2
unnamed: L7.1, USB1.P$2 (G1), USB1.P$3 (G2), USB1.P$6 (G3), USB1.P$8 (G1), USB1.P$10 (G2), USB1.S1 (SH1), USB1.S2 (SH2), USB1.S3 (SH3), USB1.S4 (SH4)
unnamed: IC3.1 (FB), R28.1, R29.2
unnamed: IC3.17 (EN), R30.2
unnamed: IC3.18 (AAM), R31.2
PA28_USB_HOST_EN: R11.2; also elsewhere on the board
PWRIN: D1.A, R39.2, TP_PWRIN.X, TVS1.K (KA), X1.2; also elsewhere on the board
TARGET_USB_N: USB1.2 (D-), Z6.1; also elsewhere on the board
TARGET_USB_P: USB1.3 (D+), Z5.1; also elsewhere on the board
USBVCC: C27.+, C35.+, F2.1, R14.2, TR1.1 (D)
VIN: C16.+, IC3.16 (VIN), L5.2, R30.1
XUSB: C26.1, F2.2, USB1.1 (VUSB)

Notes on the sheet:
USB AB
R34 NON MONTARE
R36,R37 NON MONTARE
Author: E.Vita

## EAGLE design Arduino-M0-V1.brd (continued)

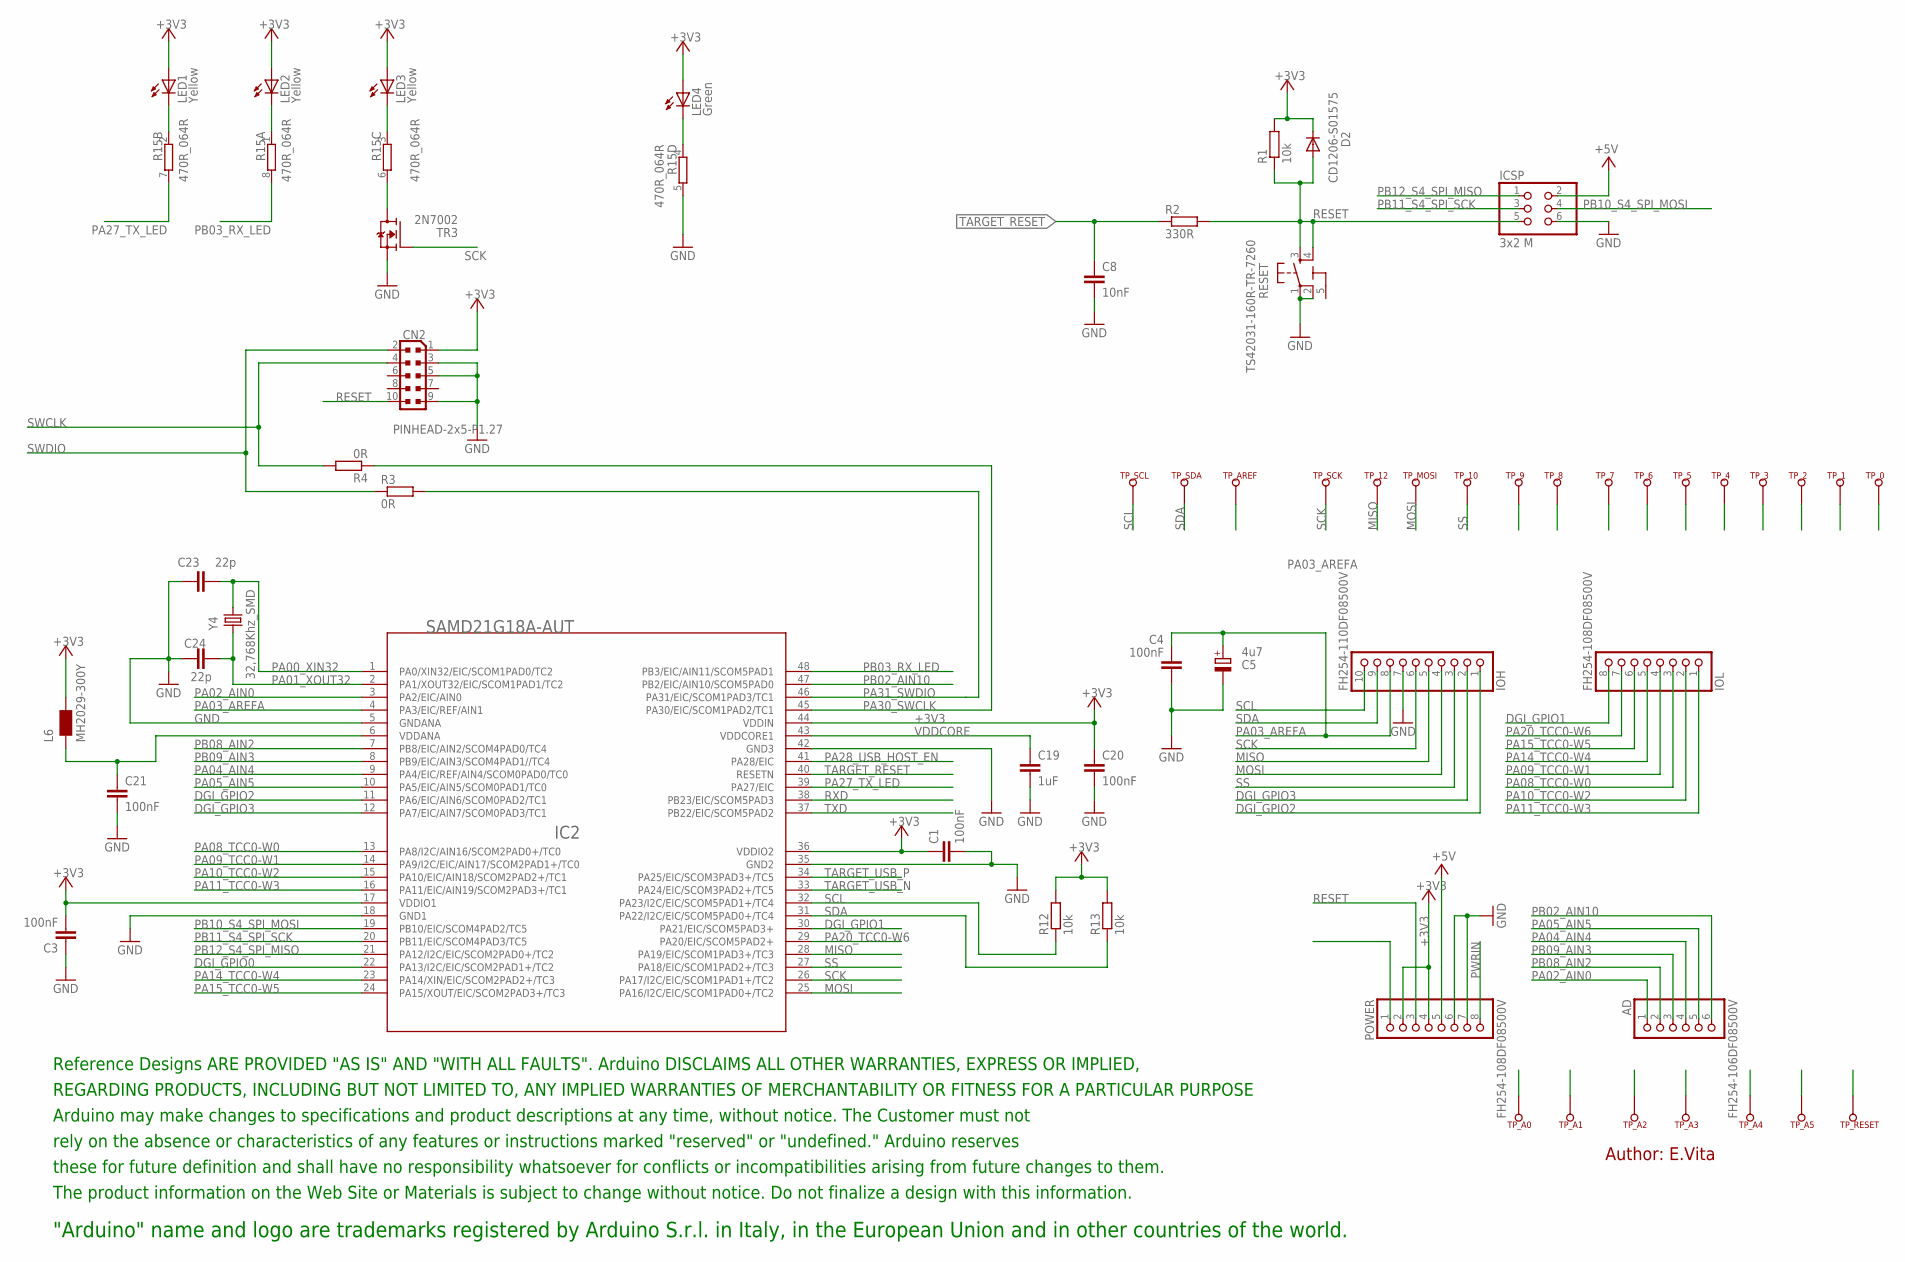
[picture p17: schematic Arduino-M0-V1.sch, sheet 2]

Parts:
AD: FH254-106DF08500V; 1X06
C1, C3, C4, C20, C21: 100nF; C0603-ROUND
C5: 4u7; SMC_A
C8: 10nF; C0603-ROUND
C19: 1uF; C0603-ROUND
C23, C24: 22p; C0603-ROUND
CN2: PINHEAD-2x5-P1.27; PINHEAD_2X05_127
D2: CD1206-S01575; MINIMELF
IC2: SAMD21G18A-AUT; TQFP48-7X7
ICSP: 3x2 M; 2X03
IOH: FH254-110DF08500V; 1X10
IOL: FH254-108DF08500V; 1X08
L6: MH2029-300Y; 0805
LED1, LED2, LED3: Yellow; CHIPLED_0805
LED4: Green; CHIPLED_0805
POWER: FH254-108DF08500V; 1X08
R1, R12, R13: 10k; R0603-ROUND
R2: 330R; R0603-ROUND
R3, R4: 0R; R0603-ROUND
R15: 470R_064R; CAY16
RESET: TS42031-160R-TR-7260; TS42
TP_0, TP_1, TP_2, TP_3, TP_4, TP_5, TP_6, TP_7, TP_8, TP_9, TP_10, TP_12: TP_SP; TP-SP
TP_A0, TP_A1, TP_A2, TP_A3, TP_A4, TP_A5: TP_SP; TP-SP
TP_AREF: TP_SP; TP-SP
TP_MOSI: TP_SP; TP-SP
TP_RESET: TP_SP; TP-SP
TP_SCK: TP_SP; TP-SP
TP_SCL: TP_SP; TP-SP
TP_SDA: TP_SP; TP-SP
TR3: 2N7002; SOT-23
U$2: DISCLAIMER-SMALL; DISCLAIMER
Y4: 32,768Khz_SMD; RESONATOR_EPSON_FC_145

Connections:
5-GND: RESET.5 (5-GND)
+3V3: C1.1, C3.2, C20.1, CN2.1, D2.C, IC2.17 (VDDIO1), IC2.36 (VDDIO2), IC2.44 (VDDIN), L6.2, LED1.A, LED2.A, LED3.A, LED4.A, POWER.2, POWER.4, R1.2, R12.2, R13.2; also elsewhere on the board
+5V: ICSP.2, POWER.5; also elsewhere on the board
DGI_GPIO0: IC2.22 (PA13/I2C/EIC/SCOM2PAD1+/TC2)
DGI_GPIO1: IC2.30 (PA21/EIC/SCOM5PAD3+), IOL.8, TP_7.X
DGI_GPIO2: IC2.11 (PA6/EIC/AIN6/SCOM0PAD2/TC1), IOH.1, TP_8.X
DGI_GPIO3: IC2.12 (PA7/EIC/AIN7/SCOM0PAD3/TC1), IOH.2, TP_9.X
GND: C1.2, C3.1, C4.2, C5.-, C8.2, C19.2, C20.2, C21.2, C23.1, C24.1, CN2.3, CN2.5, CN2.9, IC2.5 (GNDANA), IC2.18 (GND1), IC2.35 (GND2), IC2.42 (GND3), ICSP.6, IOH.7, POWER.6, POWER.7, R15.5 (2), RESET.1, RESET.2, TR3.2 (S); also elsewhere on the board
MISO: IC2.28 (PA19/EIC/SCOM1PAD3+/TC3), IOH.5, TP_12.X
MOSI: IC2.25 (PA16/I2C/EIC/SCOM1PAD0+/TC2), IOH.4, TP_MOSI.X
unnamed: LED1.C, R15.2 (1)
unnamed: LED2.C, R15.1
unnamed: LED3.C, R15.3 (1)
unnamed: LED4.C, R15.4 (1)
unnamed: R15.6 (2), TR3.1 (D)
unnamed: C21.1, IC2.6 (VDDANA), L6.1
PA00_XIN32: C23.2, IC2.1 (PA0/XIN32/EIC/SCOM1PAD0/TC2), Y4.P$2 (2)
PA01_XOUT32: C24.2, IC2.2 (PA1/XOUT32/EIC/SCOM1PAD1/TC2), Y4.P$1 (1)
PA02_AIN0: AD.1, IC2.3 (PA2/EIC/AIN0), TP_A0.X
PA03_AREFA: C4.1, C5.+, IC2.4 (PA3/EIC/REF/AIN1), IOH.8, TP_AREF.X
PA04_AIN4: AD.4, IC2.9 (PA4/EIC/REF/AIN4/SCOM0PAD0/TC0), TP_A3.X
PA05_AIN5: AD.5, IC2.10 (PA5/EIC/AIN5/SCOM0PAD1/TC0), TP_A4.X
PA08_TCC0-W0: IC2.13 (PA8/I2C/AIN16/SCOM2PAD0+/TC0), IOL.3, TP_2.X
PA09_TCC0-W1: IC2.14 (PA9/I2C/EIC/AIN17/SCOM2PAD1+/TC0), IOL.4, TP_3.X
PA10_TCC0-W2: IC2.15 (PA10/EIC/AIN18/SCOM2PAD2+/TC1), IOL.2, TP_1.X
PA11_TCC0-W3: IC2.16 (PA11/EIC/AIN19/SCOM2PAD3+/TC1), IOL.1, TP_0.X
PA14_TCC0-W4: IC2.23 (PA14/XIN/EIC/SCOM2PAD2+/TC3), IOL.5, TP_4.X
PA15_TCC0-W5: IC2.24 (PA15/XOUT/EIC/SCOM2PAD3+/TC3), IOL.6, TP_5.X
PA20_TCC0-W6: IC2.29 (PA20/EIC/SCOM5PAD2+), IOL.7, TP_6.X
PA27_TX_LED: IC2.39 (PA27/EIC), R15.7 (2)
PA28_USB_HOST_EN: IC2.41 (PA28/EIC); also elsewhere on the board
PA30_SWCLK: IC2.45 (PA30/EIC/SCOM1PAD2/TC1), R4.1
PA31_SWDIO: IC2.46 (PA31/EIC/SCOM1PAD3/TC1), R3.2
PB02_AIN10: AD.6, IC2.47 (PB2/EIC/AIN10/SCOM5PAD0), TP_A5.X
PB03_RX_LED: IC2.48 (PB3/EIC/AIN11/SCOM5PAD1), R15.8 (2)
PB08_AIN2: AD.2, IC2.7 (PB8/EIC/AIN2/SCOM4PAD0/TC4), TP_A1.X
PB09_AIN3: AD.3, IC2.8 (PB9/EIC/AIN3/SCOM4PAD1//TC4), TP_A2.X
PB10_S4_SPI_MOSI: IC2.19 (PB10/EIC/SCOM4PAD2/TC5), ICSP.4
PB11_S4_SPI_SCK: IC2.20 (PB11/EIC/SCOM4PAD3/TC5), ICSP.3
PB12_S4_SPI_MISO: IC2.21 (PA12/I2C/EIC/SCOM2PAD0+/TC2), ICSP.1
PWRIN: POWER.8; also elsewhere on the board
RESET: CN2.10, D2.A, ICSP.5, POWER.3, R1.1, R2.2, RESET.3, RESET.4, TP_RESET.X
RXD: IC2.38 (PB23/EIC/SCOM5PAD3)
SCK: IC2.26 (PA17/I2C/EIC/SCOM1PAD1+/TC2), IOH.6, TP_SCK.X, TR3.3 (G)
SCL: IC2.32 (PA23/I2C/EIC/SCOM5PAD1+/TC4), IOH.10, R12.1, TP_SCL.X
SDA: IC2.31 (PA22/I2C/EIC/SCOM5PAD0+/TC4), IOH.9, R13.1, TP_SDA.X
SS: IC2.27 (PA18/EIC/SCOM1PAD2+/TC3), IOH.3, TP_10.X
SWCLK: CN2.4, R4.2
SWDIO: CN2.2, R3.1
TARGET_RESET: C8.1, IC2.40 (RESETN), R2.1
TARGET_USB_N: IC2.33 (PA24/EIC/SCOM3PAD2+/TC5); also elsewhere on the board
TARGET_USB_P: IC2.34 (PA25/EIC/SCOM3PAD3+/TC5); also elsewhere on the board
TXD: IC2.37 (PB22/EIC/SCOM5PAD2)
VDDCORE: C19.1, IC2.43 (VDDCORE1)

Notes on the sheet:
Author: E.Vita

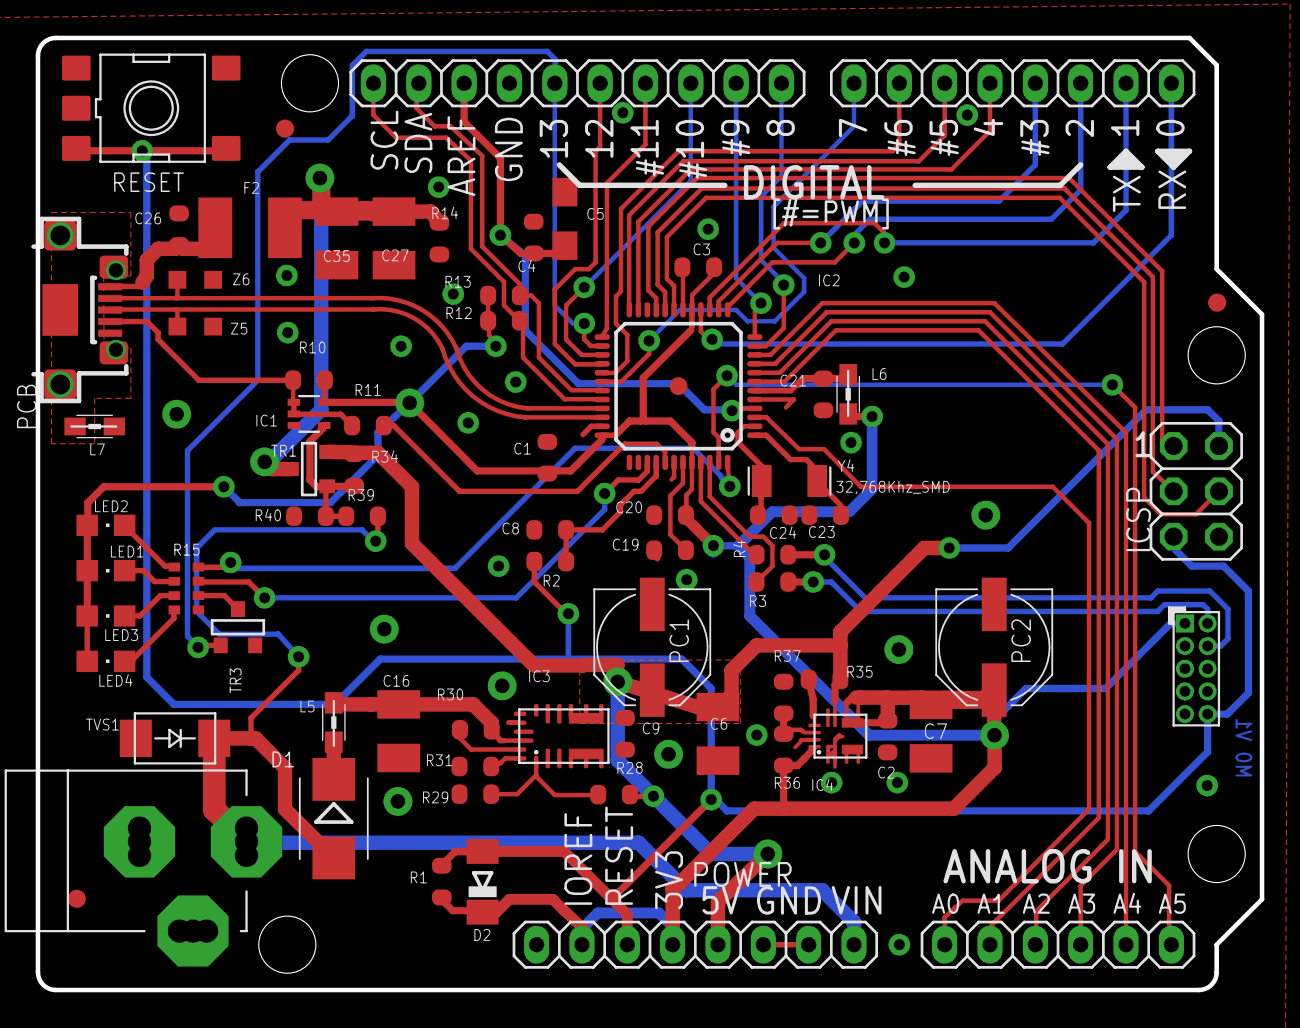
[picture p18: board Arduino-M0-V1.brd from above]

Board: 4 copper layers, 68.6 x 53.3 mm, 101 parts (0 on the bottom side), 62 nets.

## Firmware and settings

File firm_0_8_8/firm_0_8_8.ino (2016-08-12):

//////////////////////////////////////////////////////////////////////////////////////////////////////////
/* Codigo para el control del proyector de cine de 16mm modificado segun proyecto de Xavi Hurtado V2.

El control se compone de dos partes: para el motor de arrastre se utiliza una placa Trinamic TMCM-1630 con comunicacion
RS-232, para los motores de los obturadores y la comunicacion un Arduino Zero (procesador M0). Para la comunicacion
utilizamos una mochila Ethernet2 con basada el W5500 WIZnet y para la potencia en los motores de los obturadores una
mochila Pololu dual MC33926.

La distribucion I/O es la siguiente:
0,1 - serial tll utilizado para comunicacion con la placa de control Trinamic
2 - habilitacion de PWM de salidad de la placa Pololu
7 - interrupcion para el control de velocidad del motor del obturador trasero
4 - control de la direccion de giro del motor del obturador trasero
5 - interrupcion para el control de velocidad del motor del oburador frontal
6 - control de la direccion de giro del motor del obturador frontal
3 - interrupcion para el control del tiempo diferencial del oburador trasero
8 - interrupcion para el control del tiempo diferencial del oburador frontal
9 - interrupcion para el control del tiempo diferencial del arrastre de cinta
10 - utilizado por Ethernet2 CS
11 - PWM a 22kHz, 11 bits para alimentacion del motor del obturador frontal
12 - PWM a 22kHz, 11 bits para alimentacion del LED de iluminacion
13 - PWM a 22kHz, 11 bits para alimentacion del motor del obturador trasero
A0 - entrada del sensor de corriente de la placa Pololu para el motor del obturador frontal
A1 - entrada del sensor de corriente de la placa Pololu para el motor del obturador trasero

La comunicacion se hace a traves de ethernet con protocolo UDP, la IP local es 172.26.100.172 se recibe por el
puerto 8000 y se responde en el puerto 6000.
Los datos a recibir son (UDP message: string-identificador, float o int-valor a recibir):

/Luz                  - potencia enviada a la lampara LED - int 0..255
/Vel_main   - velocidad que se pretende del motor de traccion de la cinta - int o float -43~43 en fps (frames por segundo)
/Vel_front  - velocidad que se pretende del obturador frontal en OPS (obturaciones por segundo) - 0~150
/Vel_tras   - velocidad que se pretende del obturador frontal en OPS - 0~150

datos devueltos cada 100mS:

/vel_obt_tras_act     - velocidad actual del obturador trasero en OPS
/vel_obt_front_act    - velocidad actual del obturador frontal en OPS
/ph_diff_main_front   - diferencia de fase del obturador frontal con respecto a su maestro - 0~360º
/ph_diff_main_tras    - diferencia de fase del obturador trasero con respecto a su maestro - 0~360º
/frame_count	      - cuenta actual de frames desde el momento del inicio

Descripcion del sistema de control de los motores que mueven los obturadores:
El bloque de control basico es un sistema de lazo cerrado alimentando un PID con la velocidad deseada y la velocidad actual
medida en la interrupcion correspondiente (estas interrupciones tienen una tasa de 11 pulsos por revolucion y son medidas en la polea
solidaria con el motor en cuestion), la salida de PID es aplicada al PWM que alimenta el puente H de cada motor.
El siguiente nivel de control es un segundo lazo de realimentacion que tiene como entrada el resultado de la diferencia de tiempo entre
el motor que sera esclavizado y su maestro, la salida se suma a la entrada de PID, en este caso los parametros Ki, Kp y Kd
de PID estaran ajustados en una relacion aproximada 22:1 integral con respecto a proporcional, conformando un filtro de
paso bajo. Si pensamos en el motor como un oscilador controlado por voltaje (PWM), la medicion de diferencia de tiempo es
efectivamente un comparador de fase y la PID ajustada como filtro de paso bajo, el conjunto se puede ver como un PLL.
Uno de los tiempos que entran en el comparador de fase se multiplicara por un factor (/Mul_front y /Mul_tras respectivamente)
para obtener una velocidad multiplicada como resultado pudiendo controlar de esta manera velocidades relativas al master diferentes
a la unidad.
Un tercer lazo de realimentacion existe entre, la diferencia del tiempo medido directamente en cada obturador y el medido en
quien sea su master, esta diferencia es expresada en grados (0~360) y sumada al tiempo que se le resta del maestro para obtener
el error de la comparacion de entrada a PID, manejando una peticion de error en ese valor (entradas /Ph_f_target y /Ph_t_target)
conseguiremos un 'angulo' sumado al de referencia que proporciona el maestro. Este angulo se supervisa en el main loop y se corrige
cuando se obtiene el valor de tiempo en cuestion.
Para seleccionar los estados se han colocado switches logicos con los que se permite seleccionar el origen de datos para el esclavo
(/Master_tras front y /Master_front_tras) y si el motor en cuestion es libre o esclavo (/Front_free y /Tras_free), si el motor es
libre el control sera su entrada de peticion de velocidad (/Vel_front y /Vel_tras)


Escrito por Alejandro Bizzotto en 2015-16.


variables asignadas

nombre || uso


///////////////////////////////////////////////****************//////////////////////////////////////////////////

#include <SPI.h>               // needed for Arduino versions later than 0018
#include <Ethernet2.h>         // como estamos utilizando el W5500 necesitamos ethernet2 
#include <EthernetUdp2.h>      // UDP library from: bjoern@cs.stanford.edu 12/30/2008  
#include <PID_v1.h>            // PID library: http://playground.arduino.cc/Code/PIDLibrary  -doubles cambiados a floats, sample time en uS
#include <OSCMessage.h>        // para trabajar mas facilmente el intercambio de datos por udp los formatearemos en OSC, https://github.com/CNMAT/OSC

#define UDP_TX_PACKET_MAX_SIZE 28 // amplio el buffer a 28 bytes para evitar la necesidad de fragmentacion

// MAC address and IP address
byte mac[] = { 0xDE, 0xAD, 0xBE, 0xEF, 0xFE, 0xED};
IPAddress ip(172, 26, 100, 177);
char packetBuffer[UDP_TX_PACKET_MAX_SIZE]; //buffer to hold incoming packet,
EthernetUDP Udp;  // An EthernetUDP instance

volatile unsigned long new_time_mot_tras, old_time_mot_tras, new_time_mot_front, old_time_mot_front, old_time_main, new_time_main, last_sample_time_front,
         last_sample_time_tras, tick_front_act, tick_front_ant, tick_tras_act, tick_tras_ant, abs_time_obt_front, abs_time_obt_tras, abs_time_mot_tras,
         abs_time_mot_front, new_time_obt_front, old_time_obt_front, new_time_obt_tras, old_time_obt_tras;
volatile boolean time_report_mot_tras = 1, time_report_mot_front = 1, time_report_main = 0, time_report_obt_front = 0, time_report_obt_tras = 0;
volatile long act_time_mot_front = 1, act_time_mot_tras = 1, act_time_main = 1, act_time_obt_front = 1, act_time_obt_tras = 1;
volatile boolean tras_free = 1, master_tras_front, master_front_tras, front_free = 1, tras_call_int = 0, front_call_int = 0;
volatile float error_front_main = 1.0, error_tras_main = 1.0, error_front_tras = 1.0, error_tras_front = 1.0, ph_diff_main_front, ph_diff_main_tras,
               time_diff_main_front, time_diff_main_tras, time_diff_tras_front, time_diff_front_tras, ph_diff_tras_front, ph_diff_front_tras, reg;

const float prop_mot = 180.441E3, prop_mot_2 = 90220.5;      // factor de conversion tiempo_entre_pulsos vs ops (obturaciones por segundo)

int old_time_deb = 0;                         // para el control del tiempo al enviar datos
int time_front_fwd, time_front_rwd, fwd_rwd_front, time_tras_fwd, time_tras_rwd, fwd_rwd_tras, curr_tras, curr_front, frame_count = 0, time_send,
    time_front_no_int, time_tras_no_int, count_front = 0, time_tras_park, duty_t_high, time_front_park, duty_f_high;
float fino = 1.0, fino2 = 1.0, mul_front = 1.0, mul_tras = 1.0, vel_main, ph_f_target = 140.0, ph_t_target = 170.0;
// los obturadores pasan por el lado superior de la pantalla en estos angulos con respecto a
// la señal que sincroniza main, siendo el tiempo inmediato al flanco de subida de la señal
// del main el momento en el que se ha depositado un cuadro de la cinta en su sitio, por lo que
// podemos decir que en estos angulos esta sincronizado en una proyeccion normal de 2 obturaciones
// por frame
boolean leido = 1, new_vel_main_target, tras_park = 0, front_park = 0, main_run_l, main_run_r, tras_pol_sel, front_pol_sel;
byte count = 0;
char command[9], response[9];

// instancias PID
//     consigna recibida,  velocidad actual, resultado de PID
float vel_obt_tras_target, vel_obt_tras_act, pwm_mot_obt_tras;
//   factor proporcional, f. integral,       f. derivado
float Kp_obt_tras = 10.0, Ki_obt_tras = 50.0, Kd_obt_tras = 4.7E-4;  // por defecto la configuracion de PID es relajada
//                    entrada            salida             consigna
PID vel_obt_tras_PID(&vel_obt_tras_act, &pwm_mot_obt_tras, &vel_obt_tras_target, Kp_obt_tras, Ki_obt_tras, Kd_obt_tras, DIRECT); // motor del obturador trasero

float vel_obt_front_target, vel_obt_front_act, pwm_mot_obt_front, buff;
float Kp_obt_front = 10.0, Ki_obt_front = 50.0, Kd_obt_front = 4.7E-4;
PID vel_obt_front_PID(&vel_obt_front_act, &pwm_mot_obt_front, &vel_obt_front_target, Kp_obt_front, Ki_obt_front, Kd_obt_front, DIRECT); // motor del obturador frontal

void setup() {

  pinMode(2, OUTPUT); // aqui conecto la habilitacion del pwm de salida
  pinMode(4, OUTPUT); // seleccion de direccion de giro del motor del obturador trasero
  pinMode(6, OUTPUT); // seleccion de direccion de giro del motor del obturador frontal
  pinMode(3, INPUT);  // sensor optico para la posicion de parking y correccion de fase en obturador trasero
  pinMode(8, INPUT);  // sensor optico para la posicion de parking y correccion de fase en obturador frontal
  pinMode(A5, OUTPUT); // debug
  pinMode(A0, INPUT);  // sensor de corriente para el motor del obturador frontal
  pinMode(A1, INPUT);  // sensor de corriente para el motor del obturador trasero

  // start the Ethernet and UDP:
  Ethernet.begin(mac, ip);
  Udp.begin(8000);
  Serial5.begin(57600);      // con la placa Trinamic nos comunicaremos por serie
  // SerialUSB.begin(57600);

  attachInterrupt(7, time_control_mot_tras, RISING);   // interrupcion en pin 3 para el lector optico de velocidad en el motor del obturador trasero
  attachInterrupt(3, time_control_obt_tras, RISING);   // interrupcion en pin 3 para el lector optico de fase en el obturador trasero
  attachInterrupt(5, time_control_mot_front, RISING);  // interrupcion en pin 5 para el lector optico de velocidad en el motor del obturador delantero
  attachInterrupt(8, time_control_obt_front, RISING);  // interrupcion en pin 8 para el lector optico de fase en el obturador frontal
  attachInterrupt(9, time_control_main, RISING);       // interrupcion en pin 9 para el lector optico de fase en motor de arrastre
  
  analogWrite (13, 0);   // preparo las salidas de pwm en pines 13 y 11 para luego escribir directamente en sus registros
  analogWrite(12, 0);    // 12 utiliza TC3 WO1, el prescaler lo cambiare luego de llamar a analogWrite del pin 4 a DIV8 para tener ~170Hz
  analogWrite(11, 0);    // 13 y 11 utilizan TCC2, 11 bits de resolucion y ~23kHz
  REG_TCC2_PER = 0x800;

  analogWrite(4, 0);     // 4 utiliza TC3 WO0
  REG_TC3_CTRLA &= ~TCC_CTRLA_ENABLE;
  while (REG_TC3_STATUS == TC_STATUS_SYNCBUSY);
  REG_TC3_CTRLA |= TCC_CTRLA_PRESCALER_DIV64;    // frecuencia del pwm de salida ~ 3kHz
  REG_TC3_CTRLA |= TCC_CTRLA_ENABLE;
  while (REG_TC3_STATUS == TC_STATUS_SYNCBUSY);

  analogWrite(6, 0);     // 6 utililiza TCC0 WO6
  REG_TCC0_CTRLA &= ~TC_CTRLA_ENABLE;
  while (REG_TCC0_SYNCBUSY == TCC_SYNCBUSY_STATUS);
  REG_TCC0_CTRLA |= TC_CTRLA_PRESCALER_DIV256;    // frecuencia del pwm de salida ~ 90Hz
  REG_TCC0_CTRLA |= TC_CTRLA_ENABLE;
  while (REG_TCC0_SYNCBUSY == TCC_SYNCBUSY_STATUS);
  REG_TCC0_PER = 0x800;


  vel_obt_tras_PID.SetOutputLimits(0, 2048);  // el PWM de salida es de 11 bits
  vel_obt_tras_act = 1;                      // cualquier cosa que no sea 0 aqui
  vel_obt_tras_PID.SetMode(AUTOMATIC);      // si no esta automatic esta manual
  vel_obt_tras_PID.SetSampleTime(1);       // sampletime minimo, luego se asignara dinamicamente

  vel_obt_front_PID.SetOutputLimits(0, 2048);
  vel_obt_front_act = 1;
  vel_obt_front_PID.SetMode(AUTOMATIC);
  vel_obt_front_PID.SetSampleTime(1);

}

void loop() {

  int period_105_front = int (prop_mot / vel_obt_front_target * float(1.05));  // 105% periodo de motor frontal
  if (!vel_obt_front_target) period_105_front = 0.2;                           // si vel_obt_xxx_target == 0 el tiempo anterior para la comparacion es infinito y nunca entra
  if (((micros() - time_front_no_int) > period_105_front) && (!front_park)) {  // ha pasado el 105% del periodo del motor frontal
    time_front_no_int = micros();
    if (tick_front_act == tick_front_ant) {                             // y la interrupcion no se ha producido
      act_time_mot_front += int(prop_mot_2 / vel_obt_front_target);     // entonces digo que el periodo es mas alto de lo que debiera, incrementandolo en cada iteracion
      vel_obt_front_pid_comp();                                         // y llamo a PID
      front_call_int = 1;                                               // levanto la bandera para que no se llame en la proxima interrupcion
    }
    else {
      tick_front_ant = tick_front_act;    // si se ha producido la interrupcion, igualo los valores para el siguiente intervalo de periodo
      front_call_int = 0;                 // bajo la bandera para poder llamar a PID en la interrupcion
    }
  }

  /*
     las inercias del sistema hacen que la medida de tiempo en la interrupcion pueda ser erronea en velocidades bajas por falta de torque,
     para saberlo voy a poner un contador incrementado en la interrupcion (tick_front_act y tick_tras_act), que en un tiempo 5% superior
     al periodo que habria de tener (prop_mot/vel_obt_xxx_target * float(1.05)) voy a comparar con su valor anterior, si son iguales es que no se ha
     producido la interrupcion en ese tiempo, si ademas la bandera de la ultima llamada de vel_obt_xxx_comp (xxx_call_int) no se ha levantado en
     la interrupcion es que puedo llamarla aqui
     en ese caso llamare a vel_obt_xxx_comp con un valor de periodo (act_time_mot_xxx) mas alto del teorico para que PID entregue mas torque y
     corrija en la siguiente segunda interrupcion
   */
  int period_105_tras = int (prop_mot / vel_obt_tras_target * float(1.05));
  if (!vel_obt_tras_target) period_105_tras = 0.2;
  if (((micros() - time_tras_no_int) > period_105_tras) && (!tras_park)) {
    time_tras_no_int = micros();
    if (tick_tras_act == tick_tras_ant) {
      act_time_mot_tras += int(prop_mot_2 / vel_obt_tras_target);
      vel_obt_tras_pid_comp();
      tras_call_int = 1;
    }
    else {
      tick_tras_ant = tick_tras_act;
      tras_call_int = 0;
    }
  }

  OSCMessage msg_in;
  int size_packet;

  //receive a message
  if ( (size_packet = Udp.parsePacket()) > 0)
  {
    uint8_t packetBuffer[UDP_TX_PACKET_MAX_SIZE];      // esta funcion tarda ~500uS, la funcion del ejemplo: while(size--) msg.fill(Udp.read());
    Udp.read(packetBuffer, UDP_TX_PACKET_MAX_SIZE);    // tarda 6mS!!!
    msg_in.fill(packetBuffer, UDP_TX_PACKET_MAX_SIZE);
    // si la porcion string coincide, obtengo el integer o float y lo asigno a cada una de las variables de destino
    if (msg_in.match("/Luz")) {
      int val =  msg_in.getInt(0);
      if (val > 254) val = 254;
      if (val < 0) val = 0;
      REG_TC3_COUNT8_CC1 = val;          // pwm en pin 12, aqui el float no tiene sentido
      OSCMessage res ("/Luz");           // preparo respuesta con el mismo mensaje que se ha recibido
      res.add((int) val);                // y el valor numerico
      Udp.beginPacket(Udp.remoteIP(), 6000);
      res.send(Udp);                     // envio el mensaje de respuesta
      Udp.endPacket();
      res.empty();
    }

    if ((msg_in.match("/Vel_main")) && (!new_vel_main_target))        // identifico velocidad_del_motor principal
    {
      if (msg_in.isInt(0)) vel_main = msg_in.getInt(0); if (msg_in.isFloat(0)) vel_main = msg_in.getFloat(0); // si es Int me lo quedo, si es Float tambien
      const float rpm_fps = 69.45;            // cosas de las poleas y los segundos
      int val_num = abs(int(rpm_fps * vel_main));
      command[0] = 0x01;                                                          // identificacion de origen
      if (vel_main > 0 ) {
        command[1] = 0x01;  //numero de instruccion 1=ROR (rotate right), si es positivo voy a la derecha
        main_run_r = 1;
      }
      if (vel_main < 0 ) {
        command[1] = 0x02;  //numero de instruccion 2=ROL (rotate left), si es negativo voy a la izquierda
        main_run_l = 1;
      }
      if (vel_main == 0) {
        command[1] = 0x03;  //numero de instruccion 3=MST (motor stop)
        main_run_r = 0; main_run_l = 0;
      }
      command[2] = 0x00; //tipo
      command[3] = 0x00; //motor nº 0 porque es el unico

      command[4] = 0x00; // parametro de velocidad
      command[5] = 0x00; // como el maximo es 3000 los dos primeros seran cero
      command[6] = 0x00; // como la proxima escritura sera atomica, inicio a 0
      command[7] = 0x00;

      for (int n = 12; n >= 8; n--) {
        boolean foo = bitRead(val_num, n);     // leo cada uno de los bits del dato de velocidad
        if (foo) bitSet(command[6], (n - 8)); // y los escribo en el array de transmision, MSB first
      }

      for (int n = 8; n >= 0; n--) {
        boolean foo = bitRead(val_num, n);
        if (foo) bitSet(command[7], n);
      }

      int checksum = command[0];
      for (int i = 1; i < 8; i++) checksum += command[i]; // el ultimo byte del array es la suma
      command[8] = checksum;

      new_vel_main_target = 1;                            // flag para comenzar la transmision hacia la placa Trinamic
      count = 0;                                          // pointer para el array, se empieza en 0
      if (!front_free) {                                  // ante un cambio de velocidad en modo esclavo, asigno la misma velocidad para la base del calculo
        vel_obt_front_target = abs(vel_main * float(2.0));// de esta forma va mas rapido hasta ahi
      }
      if (!tras_free) {
        vel_obt_tras_target = abs(vel_main * float(2.0));
      }
    }

    if (msg_in.match("/Vel_front")) {
      if (msg_in.isInt(0)) vel_obt_front_target = msg_in.getInt(0);
      if (msg_in.isFloat(0)) vel_obt_front_target = msg_in.getFloat(0);
      if (!tras_free && master_tras_front) vel_obt_tras_target = vel_obt_front_target; // si el maestro del trasero es el frontal, igualo sus velocidades de base para ir mas rapido a la fase
        OSCMessage res ("/Vel_front");
        res.add((float) vel_obt_front_target);
        Udp.beginPacket(Udp.remoteIP(), 6000);
        res.send(Udp);
        Udp.endPacket();
        res.empty();
    }

    if (msg_in.match("/Vel_tras")) {
      if (msg_in.isInt(0)) vel_obt_tras_target = msg_in.getInt(0);
      if (msg_in.isFloat(0)) vel_obt_tras_target = msg_in.getFloat(0);
      if (!front_free && master_front_tras) vel_obt_front_target = vel_obt_tras_target;
        OSCMessage res ("/Vel_tras");
        res.add((float) vel_obt_tras_target);
        Udp.beginPacket(Udp.remoteIP(), 6000);
        res.send(Udp);
        Udp.endPacket();
        res.empty();
    }

    if (msg_in.match("/Master_front_tras")) {                         // los motores pueden ser esclavos del main o del motor del otro obturador
      if (msg_in.isInt(0)) master_front_tras = msg_in.getInt(0);
      if (msg_in.isBoolean(0)) master_front_tras = msg_in.getBoolean(0);
      OSCMessage res ("/Master_front_tras");
      res.add((boolean) master_front_tras);
      Udp.beginPacket(Udp.remoteIP(), 6000);
      res.send(Udp);
      Udp.endPacket();
      res.empty();
    }

    if (msg_in.match("/Master_tras_front")) {
      if (msg_in.isInt(0)) master_tras_front = msg_in.getInt(0);
      if (msg_in.isBoolean(0)) master_tras_front = msg_in.getBoolean(0);
      OSCMessage res ("/Master_tras_front");
      res.add((boolean) master_tras_front);
      Udp.beginPacket(Udp.remoteIP(), 6000);
      res.send(Udp);
      Udp.endPacket();
      res.empty();
    }

    if (msg_in.match("/Front_free")) {                                // cuando los obturadores son 'libres' no se enganchan en fase con nadie
      int foo = msg_in.getInt(0);                                     // y se manejaran con su control de velocidad
      if (front_free && (!foo)) {                                     // si antes era libre y se pide que sea esclavo
        if (master_front_tras) vel_obt_front_target = vel_obt_tras_act;
        else vel_obt_front_target = abs(vel_main * float(2.0));     // igualo la velocidad con su master, para ir mas rapido hasta ahi
        error_front_main = 0;
        error_front_tras = 0;
        //   Kp_obt_front = 40.0; Ki_obt_front = 900.0; Kd_obt_front = 4.7E-4;  // y ajusto PID en parametros reactivos
        // vel_obt_front_PID.SetTunings(Kp_obt_front, Ki_obt_front, Kd_obt_front);
      }
      if ((!front_free) && foo) {                                     // si antes era esclavo y se pide que sea libre
        // Kp_obt_front = 10.0; Ki_obt_front = 50.0; Kd_obt_front = 4.7E-4;
        // vel_obt_front_PID.SetTunings(Kp_obt_front, Ki_obt_front, Kd_obt_front); // ajusto PID en parametros relajados (mas estable)
      }
      front_free = foo;
      OSCMessage res ("/Front_free");
      res.add((boolean) front_free);
      Udp.beginPacket(Udp.remoteIP(), 6000);
      res.send(Udp);
      Udp.endPacket();
      res.empty();
    }
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

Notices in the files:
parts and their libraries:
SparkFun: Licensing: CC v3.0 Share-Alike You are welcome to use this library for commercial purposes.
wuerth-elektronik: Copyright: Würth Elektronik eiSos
